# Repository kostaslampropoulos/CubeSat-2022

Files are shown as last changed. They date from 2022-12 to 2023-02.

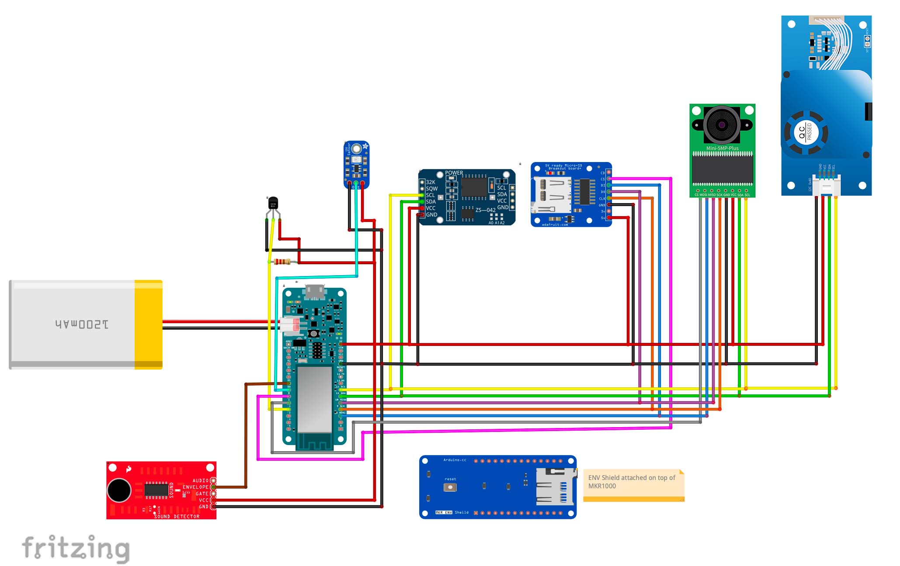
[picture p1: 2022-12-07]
Full Wiring Diagram.jpg

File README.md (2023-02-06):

# CubeSat-prototype-for-after-fire-tree-planting

2021 FIRST GLOBAL CHALLENGE: CubeSat Prototype Challenge
Team Name: Team Greece
Mission Name: Mission Dryad

1. MISSION
1.1. Defining the Mission
Due to the latest fires in Greece, both the micro-climate of many areas but also the quality of the soil have changed. Our team was deeply affected by this situation so we decided to create a CubeSat that could partly solve this problem. We suspect that the fires that happened in the summer of 2021 in Greece may have impacted the quality of the atmosphere and the soil of the burnt areas. This CubeSat is said to be able to take measurements of the temperature,the humidity, the altitude as well as the Ultraviolet radiation in the area being examined. 

What’s more, we decided to name our mission “Mission Dryad”. According to Greek mythology, the Dryads were shy spirits that dwelt deep inside forests and were also the ones responsible for their protection from unjustified human actions or wildfires.This is what we want to be: The protectors of nature and wildlife of our Homeland.

1.2. Accomplishing the Mission
When launched, the CubeSat Prototype will immediately start measuring the altitude, temperature, Ultraviolet radiation and various other particles contained in the atmosphere while also keeping track of the exact time and location this data was taken. All this data will be stored into an SD card, but it can also send its exact location and time back to the operator through a transceiver we installed. When the mission is over, we will simply pull it down and retrieve the full data. All this data will be then reviewed by experts to see in which location the atmosphere is suitable for reforestation.

2. DESIGN PROCESS
2.1. Approach
Being given the chance to create a CubeSat made us think of and recognise a problem that jeopardises our country. After brainstorming and doing various meetings we came to the conclusion that the latest fires in Greece have created a new problem; Are the burnt areas ideal enough to be reforested? This is the problem we are hoping to partly solve by creating an innovative CubeSat prototype. Taking into consideration the sensors that FIRST provided us with, we came to choose which of them would be proved useful to our project, as well as which ones we would like to further add. Our team decided to create a CubeSat that consists of a GPS to be able to track the exact position and altitude of our CubeSat, a UV sensor to measure the sun’s radiation in an area, an atmospheric pressure and a humidity sensor to note down such measurements, as well as a thermometer to check if the atmosphere’s temperature is normal. 

2.2. Prototyping
At our research we did not find any CubeSats similar to our idea so we decided to prototype ours. While making a CubeSat from scratch, we undoubtedly faced various difficulties that we got through by working as a team, taking part in the STEM talk provided by FIRST and researching through the internet. After comparing the ideas our team brainstormed, we came to the result that helping nature at this moment would be the best decision to make rather than creating other projects. We had to test our limits and make the most of the knowledge and capabilities our team had, on programming, building and creating the CubeSat.

In the programming and electrical engineering department some of the sensors used were new to us. So with a lot of practice on breadboards we managed to have a working prototype. The enclosure was designed many times and tested in simulations. The final design was selected for its stability, airflow, and endurance to shocks. The material used at first (PLA) was capable of withstanding what the CubeSat would go through so it was our final choice. 

The recovery system was simple. At first we discussed what type of parachute or parasheet we would use. After landing on the 1st option, we calculated the area the parachute needed to be so that it would land at an appropriate speed like the simulation showed the CubeSat could withstand. We concluded that a hexagon would fit best and provide enough drag and would be easy to deploy. 

2.3. Tools and Resources
As a team, for the development of our CubeSat we used multiple programming and CAD softwares, as well as physical tools. More specifically, our microcontroller was programmed using the Arduino IDE platform which uses the C/C++ language and the electronics were at first done on Fritzing. The enclosure of our Cubesat prototype was designed on Fusion 360 and Shapr 3D. The physical tools we used include a 3D 
printer, a caliper, a soldering iron and lead free solder, stainless steel screws and threaded wires. The resources used for making our CubeSat are the Arduino Forum, the FGC’s paperwork, Github as well as Stack Overflow. 
You can see the code of the CubeSat here!

3. FINAL CUBESAT PROTOTYPE DESIGN
3.1. 2021 CubeSat Prototype Kit Components
For the implementation of our experiment a variety of specific sensors were used. Firstly the 2021 CubeSat Prototype Kit provided us with the UV sensor which is using a simple analog connection, MKR ENV Shield Rev 2 for the temperature, atm pressure  and humidity which is connected directly, Real Time Clock module which is using the I2C communication protocol. This concludes the components coming from the 2021 CubeSat prototype kit. 

Each sensor had a data output and was programmed using the Arduino IDE software. All of the data was then stored in the SD card being hosted by the MKR ENV Shield Rev 2. This information was then being categorized by the software so that it would be more readable by the user and scientist analyzing them. 

Lastly, all of the sensor data is transmitted back to our computer, wirelessly and in case the CubeSat gets lost, all of the information collected does not and will be provided to the operator in no time.

3.2. Additional Components
In order to complete our CubeSat and have a complete working satellite, some added components that were not included in the 2021 CubeSat Prototype were used. 

Firstly, for the transmitting of our data, 2 transceivers were used. More specifically the RYLR 896 which uses the LoRa technology was used for it’s long range transmitting capabilities (up to 20 km) and low power consumption. AT commands were used for calibrating the ADDRESS and BAND. The frequency we used is 915 MHz, which is legal for our country. This transmitter is connected to our microcontroller using the UART communication protocol.

Another component used on our CubeSat prototype is a GPS module. This component is useful for knowing the exact coordinates and altitude of our CubeSat. The exact module is the Adafruit GPS breakout board which is connected to the microcontroller using the UART communication protocol.

3.3. Enclosure
The enclosure of our CubeSat is mostly made from 3D printable PLA with 30% infill. Each side is printed separately and then we used M6 screws to be strongly connected together. The top and bottom of the CubeSat are being held with M4 screws. Overall the enclosure was tested in Fusion 360 simulations for stress tests in case of impact and dropped from 7 meters with no visible damage. The electronics are being held by 4 wires which run along the top to the bottom of the CubeSat. The electronics are being held with 4 M4 wires with threads which also help holding the 6 pieces that the CubeSat consists of. The holes are mainly for ventilation and usability for the sensors to have a brief understanding of the environment, but the ones for the screws have special cutouts for the head of the screw to be flash with the body.  

4. LAUNCH
4.1. Technique Used
The circumstances we got to launch our CubeSat under were not ideal, so not everything went as expected. Our primary method was to deploy the CubeSat Prototype into the atmosphere by using a balloon, filled up by a bottle of helium gas. The balloon would be attached to our CubeSat making it go high enough, so that we could take all the measurements needed for our experiment. In order to prevent the loss of the CubeSat, we would attach a parachute for the touchdown.

4.2. Launch Event
Watch the launch of Mission Dryad here!
Watch our team trying out the parachute with different weights here!
Unfortunately, on the day of the launch event, it was really windy, making it impossible for the balloon to go high enough, since it was blown further away. Knowing that these days are breezy in Greece, we decided to provide ourselves with a drone in case not everything goes as planned. Luckily, one of our team’s members was able to bring one to the launch event, which under these circumstances could go higher up in the atmosphere. Therefore, our CubeSat was attached to the drone and driven up to a height of approximately 200 meters, in order to take measurements as accurately as possible. 

5. RESULTS
5.1. Results
Although we faced some difficulties during the launch event that prevented us from deploying the CubeSat as high as we intended, our mission was partly successful. The sensors attached to the CubeSat took many measurements, transmitting all of the data back to our computer wirelessly. After comparing specialists’ data to ours, we concluded that the area where we launched our CubeSat was suitable for reforestation.

5.2. Lessons Learned
We did not manage to get permission to deploy the CubeSat from the Hellenic Military. This prevented us from flying the CubeSat higher than 300 meters. Therefore, we could not take measurements from the altitude we intended to explore. That is the reason why the balloon used for deploying the CubeSat into the atmosphere had a rope attached to it. Unfortunately, due to the wind the balloon could not go as high as expected. In order to complete our mission, we decided to use a drone that could reach a height of approximately 200 meters. We believe that if we had the chance to launch our CubeSat again, after being granted permission, the balloon given would have been useful. We would have reached a higher altitude and approached the eight kilometer distance, where we could take more accurate measurements. 

5.3. FUTURE
Making a cubesat was not only a challenging but also an exciting experience! We had the chance to experiment on our project, and make the most of our skills, or even research to gain more knowledge. As for our future plans, we intend to create a simpler version of our cubesat prototype, so that students can easily recreate it low-cost, with materials that can easily be found. Making some alterations based on the needs somebody might have, would make our cubesat even more accessible to people as they could partly customise it according to their needs. If we had access to a real CubeSat and more financial resources we could also add more advanced sensors; not only to measure the atmosphere but also the soil’s properties too. Additionally, we could also add extra components to prevent wildfires from getting out of control. To conclude, our aim is to prevent wildfires from proliferating, and in case of a fire, we would be able to track whether the area being burnt is good enough to move on to reforestation.

6. REFERENCES

https://www.nasa.gov/sites/default/files/atoms/files/nasa_csli_cubesat_101_508.pdf 

https://csl.noaa.gov/factsheets/csdWildfiresFIREX.pdf

https://forum.arduino.cc

Apart from the links and resources we came across on the internet, we also communicated and elaborated on different subjects in regard to the CubeSat, with other teams from different competitions about micro satellites, like college teams from AUTH and more.

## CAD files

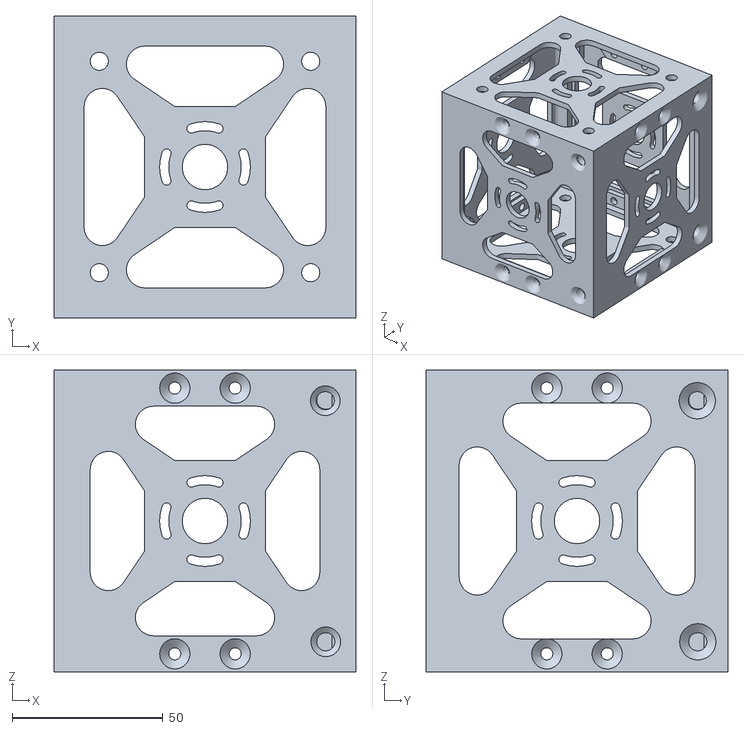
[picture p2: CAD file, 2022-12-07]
CubeSat v3.stl
100.0 x 100.0 x 100.0
